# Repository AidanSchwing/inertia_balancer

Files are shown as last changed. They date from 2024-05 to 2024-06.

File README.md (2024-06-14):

# Inertia Balancer Project

**Author:** Aidan Schwing, Sydney Ulvick

https://aidanschwing.github.io/inertia_balancer/

# Introduction
An inverted pendulum is a classic example of an unstable, controllable system in control theory. These systems are typically created using either a movable base or a moving mass to control the position of the system. We set out to implement such a system with reaction wheel-based balancing.  Initial designs of the system included a servo to brake the spinning mass in order to “bounce” up and balance. Our team was mostly interested in the control system implementation, and as such we chose to use an off-the-shelf motor controller. An ODrive derivative was ultimately chosen to serve as the BLDC driver with a 650kv quad-copter motor for price and availability. We wanted to constrain the system size to something that could serve as a display on a desk, approximately 6x6”. The final design is presented below. 

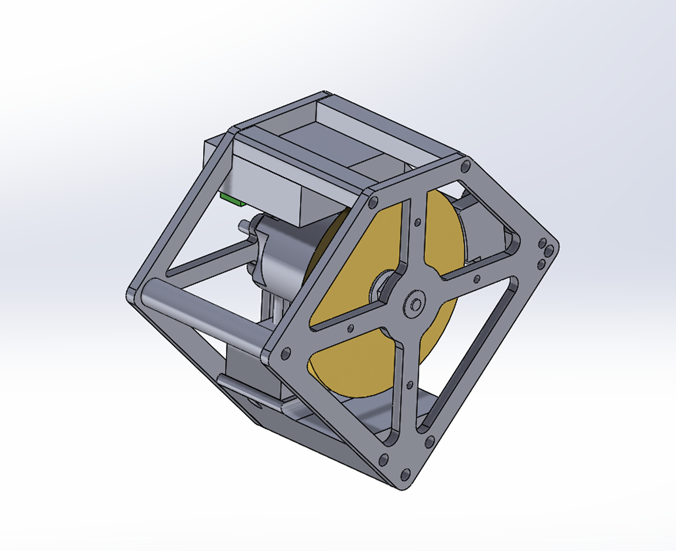
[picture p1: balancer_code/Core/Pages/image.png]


# Hardware

## Mechanical Hardware
The cube has a simple frame composed of two 3D printed sheets, separated by standoffs on four corners, fastened by M5 hardware. The inertia wheel is waterjet 6065 aluminum, post machined on the lathe to ensure concentricity with the motor shaft. The center hole was sized to ensure a light press fit on the motor shaft. The outer end of the motor shaft was turned to slide into a flanged bearing. The reaction wheel pressed into the motor shaft can be seen below, with its outer profile about to be turned to eliminate any eccentricity in the inertia.

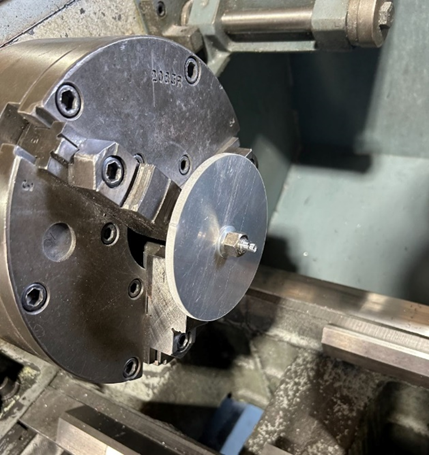
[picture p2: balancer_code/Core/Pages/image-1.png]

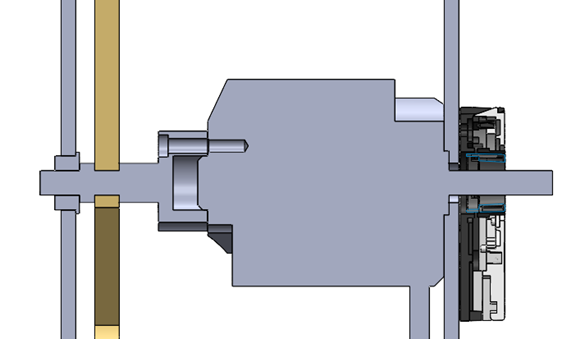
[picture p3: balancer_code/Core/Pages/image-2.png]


Motor selection was paramount for ensuring that the system would be able to output enough torque for balancing from relatively large angles. Referenced projects implement small, gimbal-style motors or extremely low kv quadcopter motors. Motor selection is interconnected with controller selection, as the controller has to be sized appropriately to meet current requirements. We settled on a 650kv quadcopter motor due to the low kv and ability to use an ODrive field-oriented-control (FOC).

Original plans for the project were to directly control wheel torque for the purposes of manipulating system angle. Torque output by the rotating wheel can be directly related to the system angle, as discussed later in the system modeling section. ODrive is an open-source system that has torque control capabilities. The ODrive’s lowest level of control occurs directly on torque, with velocity and position controls being cascaded in exterior loops. Accessing the inner loop allows us to most directly control the system. 

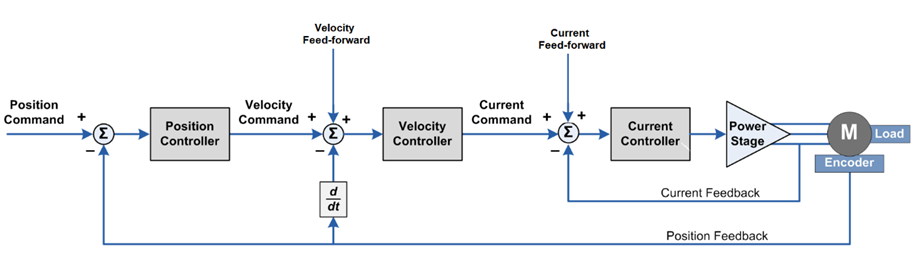
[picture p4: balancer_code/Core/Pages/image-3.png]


Upon exploration with real hardware, we discovered that the ODrive’s torque resolution is too low to control the system, driving us to use the velocity controller instead. This could potentially be resolved through use of a heavier flywheel or modifications to the controller hardware, but we did not have time to perfect the controller. 

## Electrical Hardware
To measure the angle of tilt, the ICM 20948 inertial measurement unit (IMU) was used. The imu was placed along the axis that we wanted the cube to balance along, allowing us to calculate system angle from 2 of the IMU axes. The result of this is the x direction pointing right and the y direction pointing up when the cube is upright. A depiction of the IMU orientation on the cube can be seen below. The chosen IMU has both I2C and SPI communication protocols; we chose to use I2C.  

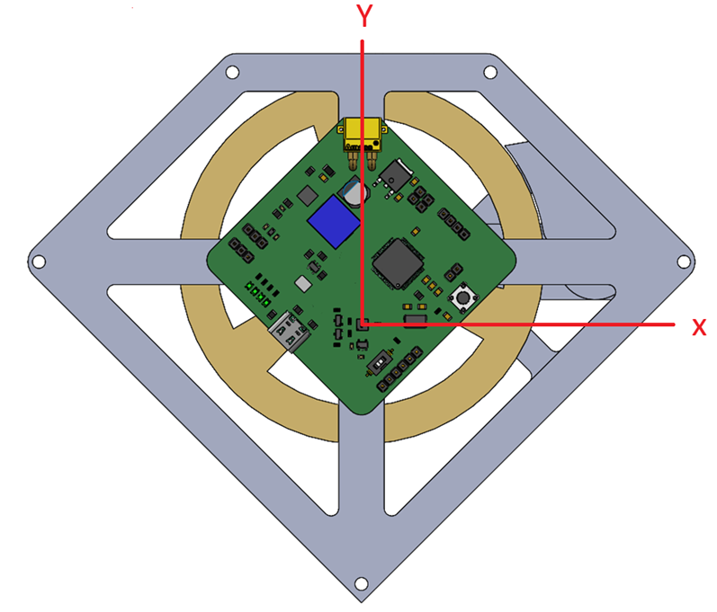
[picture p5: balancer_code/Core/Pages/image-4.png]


Interface between the motor controller and MCU PCB was accomplished with UART. This UART connection allows for reading and writing of almost every motor control parameter. Of note are direct speed and position readouts, which can be used for inputs to the LQR controller. 

The system was powered via a 4s1p, with 450 mAh, 75C max LiPO battery. The PCB was designed to interact with required sensors and motor drivers, and needed power provided appropriately. Input battery voltage (14.8V) was stepped to 5V via a buck regulator, then to 3.8V via a linear regulator for the MCU, then to 1.8V via another linear regulator for the IMU. Headers were included to power and interact with the servo, motor, motor driver, encoder, and remote e stop during troubleshooting and for worst-case if we were unable to get board power functional. Status LEDs for all voltage levels and as an MCU output were implemented. 

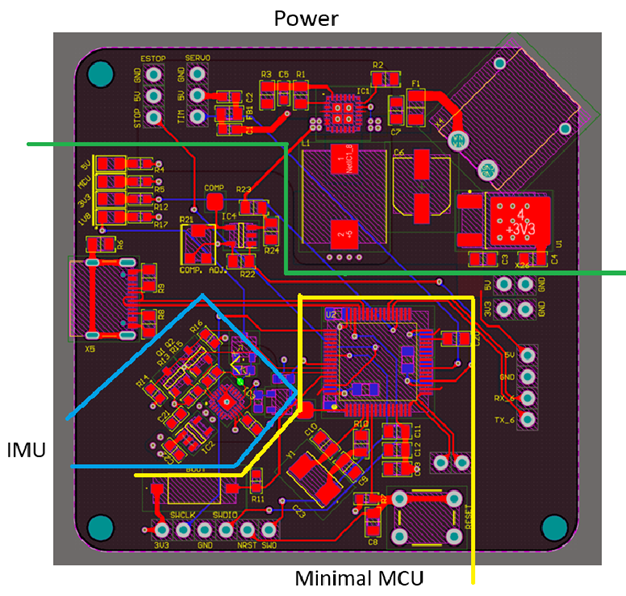
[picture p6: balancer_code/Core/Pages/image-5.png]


# Software Implementation
All code for this project was written in C. Tasks are implemented in a pseudo-state machine. The IMU state generates a new set of state variables that are used for calculation of the controller set-point in the reaction state. While they are drawn as dependent in Figure X, each of the states occurs only when a flag is set by a timer-based interrupt. Timer interrupts exist for both of the critical tasks and only raise a flag indicating that the task should be called. This ensures that the IMU read and reaction set-point recalculation occur at intervals that are approximately the same, but prevents the tasks from interrupting each other. If the set-point receives an invalid input, no speed is set. If the IMU state is missed, the control state simply outputs the same speed as the previous iteration. 

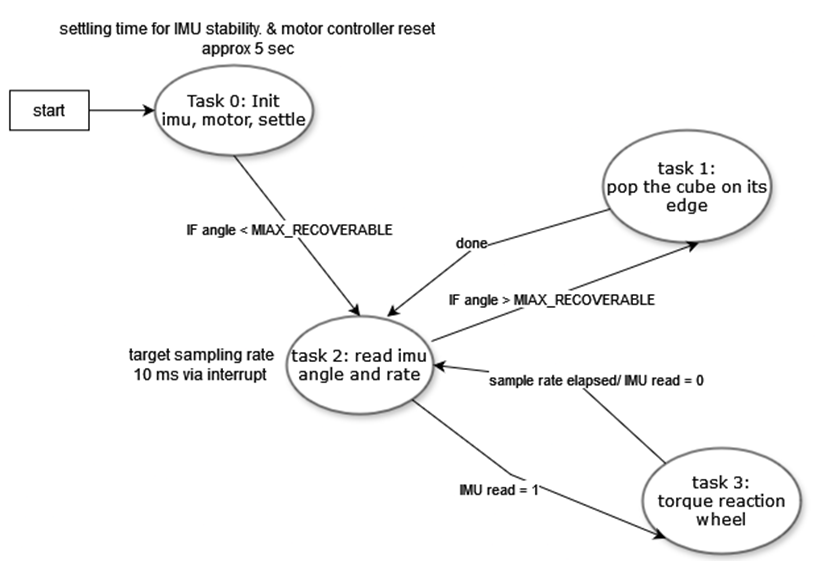
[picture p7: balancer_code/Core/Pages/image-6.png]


## IMU
An IMU driver was created from the ground up due to lack of available resources on its use with I2C. The initialization of the IMU checks the connection of the device and reads the device address. It then sends feedback through UART to a laptop. 

To best read the pitch angle, both accelerometer and gyroscope data were read. The gyroscope was read for short term accuracy but drifted through extended durations while accelerometer data was consistent but had significant noise. In order to get an accurate pitch angle over a long period of time, a complementary filter was implemented with an alpha of 0.98 on accelerometer readings. The pitch was read from the accelerometer by taking the inverse tan of the y and x components, knowing that gravity is always in the direction of negative y. The pitch from the gyro was read by integrating the value by multiplying it with the sampling rate. This setup requires the system to be “calibrated” by leaving the system near it’s zero point for approximately 3 seconds, allowing the calculated system angle to settle. 

Ultimately, it would have been easier to use an IMU with built-in euler angle calculations. 

## Motor Driver: ODrive Interface
Communication with the ODrive motor controller from a separate MCU is possible with a wide variety of protocols. The simplest of these is the [ASCII protocol](https://docs.odriverobotics.com/v/latest/manual/ascii-protocol.html) , where strings are sent in a specified format and terminated with a new-line character. This protocol allows for both writing and reading of control parameters for the BLDC. 

The ODrive also responds to some commands with specified outputs of known format. Receiving these responses is non-trivial and is performed with a callback on UART inputs that checks the length of a message buffer and for the termination character of the response. A blocking “receive” state is placed on the main code loop during message receives from the external controller, though this response period is usually negligibly short compared to other code critical code execution.  

## Control System
Multiple controllers were considered for optimally balancing. While PID control can be useful for driving the system to zero angle, it does allow for minimization of the spinning mass’s speed. An LQR controller can ideally perform multi-variate control, as the controlled variable can be treated as a function of the chosen state variables. An LQR controller can minimize system angle and wheel speed if optimized correctly. LQR controller implementation is also computationally inexpensive, as once the state variables are determined it is simply a matter of multiplying said state variables by their respective gains. 

The system was modeled using state variables of system angle, angular speed, and wheel angular speed. Due to the torque control issues mentioned in the mechanical hardware section, we switched the BLDC to control motor speed. We then can estimate the change in speed with some small time constant approximated from step tests in speed.

Once the state matrices were determined, MATLAB was used to discretize the system model and determine the LQR gains. The discretized system response appeared reasonable, but ultimately the gains failed to adequately control the system. 

Our largest issue with control was oscillations around zero angle. High penalty on system angle during LQR gain calculation results in very aggressive oscillations around the zero angle as error changes signs, while low penalty fails to adequately generate the torque required beyond a very small angle range. The system can balance for an extremely small range of angles, but further exploration into control strategies could prove beneficial to performance. Direct control over torque as originally planned would be best for system control, as the speed of the motor is not directly coupled with the system angle. 

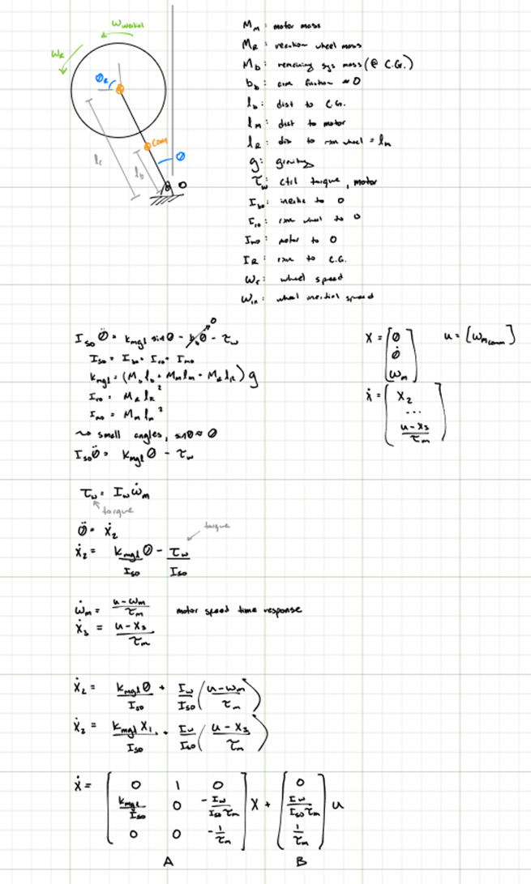
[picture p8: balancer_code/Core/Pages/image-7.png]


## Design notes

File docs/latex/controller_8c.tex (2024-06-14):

\doxysection{controller.\+c File Reference}
\hypertarget{controller_8c}{}\label{controller_8c}\index{controller.c@{controller.c}}

Provides functions relevant to system control.  

{\ttfamily \#include "{}controller.\+h"{}}\newline
{\ttfamily \#include "{}main.\+h"{}}\newline
{\ttfamily \#include $<$math.\+h$>$}\newline
Include dependency graph for controller.\+c\+:\nopagebreak
\begin{figure}[H]
\begin{center}
\leavevmode
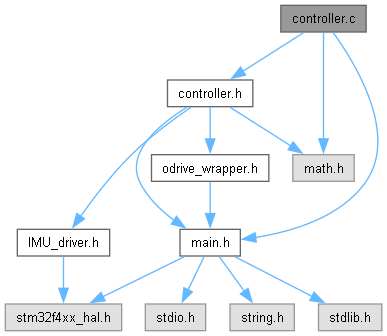
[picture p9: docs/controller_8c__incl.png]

\end{center}
\end{figure}
\doxysubsubsection*{Macros}
\begin{DoxyCompactItemize}
\item 
\#define \mbox{\hyperlink{controller_8c_a58a9c1a7ff5f19164ba9811c9fd80770}{MAX\+\_\+\+CHANGE}}~0.\+1
\begin{DoxyCompactList}\small\item\em Maximum change in controller speed setpoint per interval. \end{DoxyCompactList}\end{DoxyCompactItemize}
\doxysubsubsection*{Functions}
\begin{DoxyCompactItemize}
\item 
void \mbox{\hyperlink{controller_8c_a1bb07a75ed5a7889a5ccb8bc1ae6a9f6}{update\+\_\+control}} (\mbox{\hyperlink{structodrive__t}{odrive\+\_\+t}} \texorpdfstring{$\ast$}{*}p\+\_\+odrive, float angle, float \mbox{\hyperlink{controller_8c_acb4c2f4fbad69c2d11b5878671545191}{angular\+\_\+velocity}}, float motor\+\_\+curr\+\_\+speed)
\begin{DoxyCompactList}\small\item\em Calculates an updates the motor speed setpoint using an LQR implementation. \end{DoxyCompactList}\item 
\mbox{\hyperlink{structpos__spd}{pos\+\_\+spd}} \mbox{\hyperlink{controller_8c_a954bf1baac2fc318fb976257965a9940}{calculate\+\_\+\+IMU\+\_\+\+Angle}} (\mbox{\hyperlink{struct_i_c_m__20948}{ICM\+\_\+20948}} \texorpdfstring{$\ast$}{*}p\+\_\+\+IMU)
\begin{DoxyCompactList}\small\item\em Initializes the system angle using the IMU using a complementary filter. \end{DoxyCompactList}\end{DoxyCompactItemize}
\doxysubsubsection*{Variables}
\begin{DoxyCompactItemize}
\item 
float \mbox{\hyperlink{controller_8c_ab9495215123bd4bc532d4678cb402897}{K}} \mbox{[}3\mbox{]} = \{15, 0.\+1, -\/0.\+3\}
\begin{DoxyCompactList}\small\item\em LQR gain matrix. \end{DoxyCompactList}\item 
float \mbox{\hyperlink{controller_8c_ad50f9053a1bfede86c60be067d744d71}{x}} \mbox{[}3\mbox{]} = \{0,0,0\}
\begin{DoxyCompactList}\small\item\em State vector in form \mbox{[}angle, angular\+\_\+vel, wheel\+\_\+spd\mbox{]}. \end{DoxyCompactList}\item 
float \mbox{\hyperlink{controller_8c_a55831f7eab5ed2917a0191e858852f42}{u}} = 0
\begin{DoxyCompactList}\small\item\em Commanded motor speed. \end{DoxyCompactList}\item 
char \mbox{\hyperlink{controller_8c_a34e7004bcd98a060416abb58359410fd}{ctrl\+\_\+msg}} \mbox{[}50\mbox{]}
\item 
float \mbox{\hyperlink{controller_8c_a5be5be58449ccca7679ac2d151477f9d}{angle\+\_\+z}} = 0.\+0f
\item 
float \mbox{\hyperlink{controller_8c_acb4c2f4fbad69c2d11b5878671545191}{angular\+\_\+velocity}} = 0.\+0f
\end{DoxyCompactItemize}

\doxysubsection{Detailed Description}
Provides functions relevant to system control. 

\doxysubsection{Macro Definition Documentation}
\Hypertarget{controller_8c_a58a9c1a7ff5f19164ba9811c9fd80770}\index{controller.c@{controller.c}!MAX\_CHANGE@{MAX\_CHANGE}}
\index{MAX\_CHANGE@{MAX\_CHANGE}!controller.c@{controller.c}}
\doxysubsubsection{\texorpdfstring{MAX\_CHANGE}{MAX\_CHANGE}}
{\footnotesize\ttfamily \label{controller_8c_a58a9c1a7ff5f19164ba9811c9fd80770} 
\#define MAX\+\_\+\+CHANGE~0.\+1}

Maximum change in controller speed setpoint per interval. 

\doxysubsection{Function Documentation}
\Hypertarget{controller_8c_a954bf1baac2fc318fb976257965a9940}\index{controller.c@{controller.c}!calculate\_IMU\_Angle@{calculate\_IMU\_Angle}}
\index{calculate\_IMU\_Angle@{calculate\_IMU\_Angle}!controller.c@{controller.c}}
\doxysubsubsection{\texorpdfstring{calculate\_IMU\_Angle()}{calculate\_IMU\_Angle()}}
{\footnotesize\ttfamily \label{controller_8c_a954bf1baac2fc318fb976257965a9940} 
\mbox{\hyperlink{structpos__spd}{pos\+\_\+spd}} calculate\+\_\+\+IMU\+\_\+\+Angle (\begin{DoxyParamCaption}\item[{\mbox{\hyperlink{struct_i_c_m__20948}{ICM\+\_\+20948}} \texorpdfstring{$\ast$}{*}}]{p\+\_\+\+IMU}{}\end{DoxyParamCaption})}

Initializes the system angle using the IMU using a complementary filter. 

Calls functions from the IMU driver and calculates the system angle using a complementary filter. Noise was determined to be substantial even in the gyro data, so the gyro output is smoothed by calculating the true change in system angle. This is a little messy. 
\begin{DoxyParams}{Parameters}
{\em \doxylink{struct_i_c_m__20948}{ICM\+\_\+20948}} & Pointer to an IMU object \\
\hline
\end{DoxyParams}
\Hypertarget{controller_8c_a1bb07a75ed5a7889a5ccb8bc1ae6a9f6}\index{controller.c@{controller.c}!update\_control@{update\_control}}
\index{update\_control@{update\_control}!controller.c@{controller.c}}
\doxysubsubsection{\texorpdfstring{update\_control()}{update\_control()}}
{\footnotesize\ttfamily \label{controller_8c_a1bb07a75ed5a7889a5ccb8bc1ae6a9f6} 
void update\+\_\+control (\begin{DoxyParamCaption}\item[{\mbox{\hyperlink{structodrive__t}{odrive\+\_\+t}} \texorpdfstring{$\ast$}{*}}]{p\+\_\+odrive}{, }\item[{float}]{angle}{, }\item[{float}]{angular\+\_\+velocity}{, }\item[{float}]{motor\+\_\+curr\+\_\+speed}{}\end{DoxyParamCaption})}

Calculates an updates the motor speed setpoint using an LQR implementation. 

Calculates the next motor speed setpoint using current state vector and set of LQR gains. LQR gains originally calculated using MATLAB script. 
\begin{DoxyParams}{Parameters}
{\em p\+\_\+odrive} & Pointer to an ODrive object. \\
\hline
{\em angle} & Current system angle. \\
\hline
{\em angular\+\_\+velocity} & Current system angular velocity. \\
\hline
{\em motor\+\_\+curr\+\_\+speed} & Current motor speed. \\
\hline
\end{DoxyParams}

\doxysubsection{Variable Documentation}
\Hypertarget{controller_8c_a5be5be58449ccca7679ac2d151477f9d}\index{controller.c@{controller.c}!angle\_z@{angle\_z}}
\index{angle\_z@{angle\_z}!controller.c@{controller.c}}
\doxysubsubsection{\texorpdfstring{angle\_z}{angle\_z}}
{\footnotesize\ttfamily \label{controller_8c_a5be5be58449ccca7679ac2d151477f9d} 
float angle\+\_\+z = 0.\+0f}

\Hypertarget{controller_8c_acb4c2f4fbad69c2d11b5878671545191}\index{controller.c@{controller.c}!angular\_velocity@{angular\_velocity}}
\index{angular\_velocity@{angular\_velocity}!controller.c@{controller.c}}
\doxysubsubsection{\texorpdfstring{angular\_velocity}{angular\_velocity}}
{\footnotesize\ttfamily \label{controller_8c_acb4c2f4fbad69c2d11b5878671545191} 
float angular\+\_\+velocity = 0.\+0f}

\Hypertarget{controller_8c_a34e7004bcd98a060416abb58359410fd}\index{controller.c@{controller.c}!ctrl\_msg@{ctrl\_msg}}
\index{ctrl\_msg@{ctrl\_msg}!controller.c@{controller.c}}
\doxysubsubsection{\texorpdfstring{ctrl\_msg}{ctrl\_msg}}
{\footnotesize\ttfamily \label{controller_8c_a34e7004bcd98a060416abb58359410fd} 
char ctrl\+\_\+msg\mbox{[}50\mbox{]}}

\Hypertarget{controller_8c_ab9495215123bd4bc532d4678cb402897}\index{controller.c@{controller.c}!K@{K}}
\index{K@{K}!controller.c@{controller.c}}
\doxysubsubsection{\texorpdfstring{K}{K}}
{\footnotesize\ttfamily \label{controller_8c_ab9495215123bd4bc532d4678cb402897} 
float K\mbox{[}3\mbox{]} = \{15, 0.\+1, -\/0.\+3\}}

LQR gain matrix. 

\Hypertarget{controller_8c_a55831f7eab5ed2917a0191e858852f42}\index{controller.c@{controller.c}!u@{u}}
\index{u@{u}!controller.c@{controller.c}}
\doxysubsubsection{\texorpdfstring{u}{u}}
{\footnotesize\ttfamily \label{controller_8c_a55831f7eab5ed2917a0191e858852f42} 
float u = 0}

Commanded motor speed. 

\Hypertarget{controller_8c_ad50f9053a1bfede86c60be067d744d71}\index{controller.c@{controller.c}!x@{x}}
\index{x@{x}!controller.c@{controller.c}}
\doxysubsubsection{\texorpdfstring{x}{x}}
{\footnotesize\ttfamily \label{controller_8c_ad50f9053a1bfede86c60be067d744d71} 
float x\mbox{[}3\mbox{]} = \{0,0,0\}}

State vector in form \mbox{[}angle, angular\+\_\+vel, wheel\+\_\+spd\mbox{]}.

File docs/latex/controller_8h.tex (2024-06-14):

\doxysection{controller.\+h File Reference}
\hypertarget{controller_8h}{}\label{controller_8h}\index{controller.h@{controller.h}}
{\ttfamily \#include "{}main.\+h"{}}\newline
{\ttfamily \#include "{}IMU\+\_\+driver.\+h"{}}\newline
{\ttfamily \#include "{}odrive\+\_\+wrapper.\+h"{}}\newline
{\ttfamily \#include $<$math.\+h$>$}\newline
Include dependency graph for controller.\+h\+:\nopagebreak
\begin{figure}[H]
\begin{center}
\leavevmode
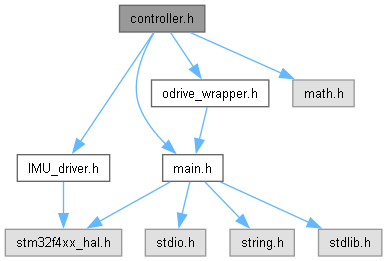
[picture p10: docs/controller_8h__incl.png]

\end{center}
\end{figure}
This graph shows which files directly or indirectly include this file\+:\nopagebreak
\begin{figure}[H]
\begin{center}
\leavevmode

\end{center}
\end{figure}
\doxysubsubsection*{Data Structures}
\begin{DoxyCompactItemize}
\item 
struct \mbox{\hyperlink{structpos__spd}{pos\+\_\+spd}}
\end{DoxyCompactItemize}
\doxysubsubsection*{Macros}
\begin{DoxyCompactItemize}
\item 
\#define \mbox{\hyperlink{controller_8h_af5abd28c44c29b7397c84f1fec4b1d84}{ALPHA}}~0.\+98
\item 
\#define \mbox{\hyperlink{controller_8h_a943f07034774ef1261d62cd0d3d1fec9}{DT}}~0.\+01
\item 
\#define \mbox{\hyperlink{controller_8h_ae13192d02ea165e8b1ac471bf287be16}{DISPLACEMENT\+\_\+\+DIST}}~0.\+07
\end{DoxyCompactItemize}
\doxysubsubsection*{Functions}
\begin{DoxyCompactItemize}
\item 
void \mbox{\hyperlink{controller_8h_a1bb07a75ed5a7889a5ccb8bc1ae6a9f6}{update\+\_\+control}} (\mbox{\hyperlink{structodrive__t}{odrive\+\_\+t}} \texorpdfstring{$\ast$}{*}p\+\_\+odrive, float angle, float \mbox{\hyperlink{controller_8c_acb4c2f4fbad69c2d11b5878671545191}{angular\+\_\+velocity}}, float motor\+\_\+curr\+\_\+speed)
\begin{DoxyCompactList}\small\item\em Calculates an updates the motor speed setpoint using an LQR implementation. \end{DoxyCompactList}\item 
\mbox{\hyperlink{structpos__spd}{pos\+\_\+spd}} \mbox{\hyperlink{controller_8h_a954bf1baac2fc318fb976257965a9940}{calculate\+\_\+\+IMU\+\_\+\+Angle}} (\mbox{\hyperlink{struct_i_c_m__20948}{ICM\+\_\+20948}} \texorpdfstring{$\ast$}{*}p\+\_\+\+IMU)
\begin{DoxyCompactList}\small\item\em Initializes the system angle using the IMU using a complementary filter. \end{DoxyCompactList}\end{DoxyCompactItemize}
\doxysubsubsection*{Variables}
\begin{DoxyCompactItemize}
\item 
struct pos\+\_\+spd \mbox{\hyperlink{controller_8h_a739745815516ab387b3bd08e33ddc4c3}{pos\+\_\+spd}}
\end{DoxyCompactItemize}

\doxysubsection{Macro Definition Documentation}
\Hypertarget{controller_8h_af5abd28c44c29b7397c84f1fec4b1d84}\index{controller.h@{controller.h}!ALPHA@{ALPHA}}
\index{ALPHA@{ALPHA}!controller.h@{controller.h}}
\doxysubsubsection{\texorpdfstring{ALPHA}{ALPHA}}
{\footnotesize\ttfamily \label{controller_8h_af5abd28c44c29b7397c84f1fec4b1d84} 
\#define ALPHA~0.\+98}

\Hypertarget{controller_8h_ae13192d02ea165e8b1ac471bf287be16}\index{controller.h@{controller.h}!DISPLACEMENT\_DIST@{DISPLACEMENT\_DIST}}
\index{DISPLACEMENT\_DIST@{DISPLACEMENT\_DIST}!controller.h@{controller.h}}
\doxysubsubsection{\texorpdfstring{DISPLACEMENT\_DIST}{DISPLACEMENT\_DIST}}
{\footnotesize\ttfamily \label{controller_8h_ae13192d02ea165e8b1ac471bf287be16} 
\#define DISPLACEMENT\+\_\+\+DIST~0.\+07}

\Hypertarget{controller_8h_a943f07034774ef1261d62cd0d3d1fec9}\index{controller.h@{controller.h}!DT@{DT}}
\index{DT@{DT}!controller.h@{controller.h}}
\doxysubsubsection{\texorpdfstring{DT}{DT}}
{\footnotesize\ttfamily \label{controller_8h_a943f07034774ef1261d62cd0d3d1fec9} 
\#define DT~0.\+01}

\doxysubsection{Function Documentation}
\Hypertarget{controller_8h_a954bf1baac2fc318fb976257965a9940}\index{controller.h@{controller.h}!calculate\_IMU\_Angle@{calculate\_IMU\_Angle}}
\index{calculate\_IMU\_Angle@{calculate\_IMU\_Angle}!controller.h@{controller.h}}
\doxysubsubsection{\texorpdfstring{calculate\_IMU\_Angle()}{calculate\_IMU\_Angle()}}
{\footnotesize\ttfamily \label{controller_8h_a954bf1baac2fc318fb976257965a9940} 
\mbox{\hyperlink{structpos__spd}{pos\+\_\+spd}} calculate\+\_\+\+IMU\+\_\+\+Angle (\begin{DoxyParamCaption}\item[{\mbox{\hyperlink{struct_i_c_m__20948}{ICM\+\_\+20948}} \texorpdfstring{$\ast$}{*}}]{p\+\_\+\+IMU}{}\end{DoxyParamCaption})}

Initializes the system angle using the IMU using a complementary filter. 

Calls functions from the IMU driver and calculates the system angle using a complementary filter. Noise was determined to be substantial even in the gyro data, so the gyro output is smoothed by calculating the true change in system angle. This is a little messy. 
\begin{DoxyParams}{Parameters}
{\em \doxylink{struct_i_c_m__20948}{ICM\+\_\+20948}} & Pointer to an IMU object \\
\hline
\end{DoxyParams}
\Hypertarget{controller_8h_a1bb07a75ed5a7889a5ccb8bc1ae6a9f6}\index{controller.h@{controller.h}!update\_control@{update\_control}}
\index{update\_control@{update\_control}!controller.h@{controller.h}}
\doxysubsubsection{\texorpdfstring{update\_control()}{update\_control()}}
{\footnotesize\ttfamily \label{controller_8h_a1bb07a75ed5a7889a5ccb8bc1ae6a9f6} 
void update\+\_\+control (\begin{DoxyParamCaption}\item[{\mbox{\hyperlink{structodrive__t}{odrive\+\_\+t}} \texorpdfstring{$\ast$}{*}}]{p\+\_\+odrive}{, }\item[{float}]{angle}{, }\item[{float}]{angular\+\_\+velocity}{, }\item[{float}]{motor\+\_\+curr\+\_\+speed}{}\end{DoxyParamCaption})}

Calculates an updates the motor speed setpoint using an LQR implementation. 

Calculates the next motor speed setpoint using current state vector and set of LQR gains. LQR gains originally calculated using MATLAB script. 
\begin{DoxyParams}{Parameters}
{\em p\+\_\+odrive} & Pointer to an ODrive object. \\
\hline
{\em angle} & Current system angle. \\
\hline
{\em angular\+\_\+velocity} & Current system angular velocity. \\
\hline
{\em motor\+\_\+curr\+\_\+speed} & Current motor speed. \\
\hline
\end{DoxyParams}

\doxysubsection{Variable Documentation}
\Hypertarget{controller_8h_a739745815516ab387b3bd08e33ddc4c3}\index{controller.h@{controller.h}!pos\_spd@{pos\_spd}}
\index{pos\_spd@{pos\_spd}!controller.h@{controller.h}}
\doxysubsubsection{\texorpdfstring{pos\_spd}{pos\_spd}}
{\footnotesize\ttfamily \label{controller_8h_a739745815516ab387b3bd08e33ddc4c3} 
struct pos\+\_\+spd pos\+\_\+spd}

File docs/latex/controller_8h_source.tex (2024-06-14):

\doxysection{controller.\+h}
\hypertarget{controller_8h_source}{}\label{controller_8h_source}\index{controller.h@{controller.h}}
\mbox{\hyperlink{controller_8h}{Go to the documentation of this file.}}
\begin{DoxyCode}{0}
\DoxyCodeLine{00001\ \textcolor{comment}{/*}}
\DoxyCodeLine{00002\ \textcolor{comment}{\ *\ controller.h}}
\DoxyCodeLine{00003\ \textcolor{comment}{\ *}}
\DoxyCodeLine{00004\ \textcolor{comment}{\ *\ \ Created\ on:\ Jun\ 8,\ 2024}}
\DoxyCodeLine{00005\ \textcolor{comment}{\ *\ \ \ \ \ \ Author:\ Aidan}}
\DoxyCodeLine{00006\ \textcolor{comment}{\ */}}
\DoxyCodeLine{00007\ }
\DoxyCodeLine{00008\ \textcolor{preprocessor}{\#ifndef\ INC\_CONTROLLER\_H\_}}
\DoxyCodeLine{00009\ \textcolor{preprocessor}{\#define\ INC\_CONTROLLER\_H\_}}
\DoxyCodeLine{00010\ }
\DoxyCodeLine{00011\ \textcolor{preprocessor}{\#include\ "{}\mbox{\hyperlink{main_8h}{main.h}}"{}}}
\DoxyCodeLine{00012\ \textcolor{preprocessor}{\#include\ "{}\mbox{\hyperlink{_i_m_u__driver_8h}{IMU\_driver.h}}"{}}}
\DoxyCodeLine{00013\ \textcolor{preprocessor}{\#include\ "{}\mbox{\hyperlink{odrive__wrapper_8h}{odrive\_wrapper.h}}"{}}}
\DoxyCodeLine{00014\ \textcolor{preprocessor}{\#include\ <math.h>}}
\DoxyCodeLine{00015\ }
\DoxyCodeLine{00016\ \textcolor{comment}{//\ defines\ for\ the\ complementary\ filter}}
\DoxyCodeLine{00017\ \textcolor{preprocessor}{\#define\ ALPHA\ 0.98}}
\DoxyCodeLine{00018\ \textcolor{preprocessor}{\#define\ DT\ 0.01\ \ \ \ \ \ \ \ \ \ \ \ \ \ \ \ \ \ \ \ \ }\textcolor{comment}{//\ sampling\ period\ 10ms}}
\DoxyCodeLine{00019\ \textcolor{preprocessor}{\#define\ DISPLACEMENT\_DIST\ 0.07\ \ \ \ \ \ }\textcolor{comment}{//\ displacement\ distance\ to\ the\ axis\ of\ the\ gyro\ that\ is}}
\DoxyCodeLine{00020\ }
\DoxyCodeLine{00021\ \textcolor{keyword}{struct\ }\mbox{\hyperlink{structpos__spd}{pos\_spd}}\ \{}
\DoxyCodeLine{00022\ \ \ \ \ \textcolor{keywordtype}{float}\ \mbox{\hyperlink{structpos__spd_a76777b356ab2a080225682528119c4fe}{position}};}
\DoxyCodeLine{00023\ \ \ \ \ \textcolor{keywordtype}{float}\ \mbox{\hyperlink{structpos__spd_a7f7e4724cf57d59513b39c5ecc81adc8}{speed}};}
\DoxyCodeLine{00024\ \}\textcolor{keyword}{typedef}\ \mbox{\hyperlink{controller_8h_a739745815516ab387b3bd08e33ddc4c3}{pos\_spd}};}
\DoxyCodeLine{00025\ }
\DoxyCodeLine{00026\ \textcolor{comment}{//\ prototype\ functions}}
\DoxyCodeLine{00027\ \textcolor{comment}{//\ LQR\ controller,\ update\ speed\ setpoint}}
\DoxyCodeLine{00028\ \textcolor{keywordtype}{void}\ \mbox{\hyperlink{controller_8h_a1bb07a75ed5a7889a5ccb8bc1ae6a9f6}{update\_control}}(\mbox{\hyperlink{structodrive__t}{odrive\_t}}\ *p\_odrive,\ \textcolor{keywordtype}{float}\ angle,\ \textcolor{keywordtype}{float}\ \mbox{\hyperlink{controller_8c_acb4c2f4fbad69c2d11b5878671545191}{angular\_velocity}},\ \textcolor{keywordtype}{float}\ motor\_curr\_speed);}
\DoxyCodeLine{00029\ \textcolor{comment}{//\ System\ angle\ using\ complementary\ filter\ on\ gyro\ and\ accel\ data}}
\DoxyCodeLine{00030\ \mbox{\hyperlink{structpos__spd}{pos\_spd}}\ \mbox{\hyperlink{controller_8h_a954bf1baac2fc318fb976257965a9940}{calculate\_IMU\_Angle}}(\mbox{\hyperlink{struct_i_c_m__20948}{ICM\_20948}}\ *p\_IMU);}
\DoxyCodeLine{00031\ }
\DoxyCodeLine{00032\ }
\DoxyCodeLine{00033\ \textcolor{preprocessor}{\#endif\ }\textcolor{comment}{/*\ INC\_CONTROLLER\_H\_\ */}\textcolor{preprocessor}{}}

\end{DoxyCode}

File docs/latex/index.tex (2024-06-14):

\chapter{reaction\+\_\+balance}
\hypertarget{index}{}\label{index}\index{reaction\_balance@{reaction\_balance}}
{\bfseries{Author\+:}} Aidan Schwing, Sydney Ulvick

{\bfseries{Date\+:}} 2024-\/06-\/14\hypertarget{index_autotoc_md0}{}\doxysection{\texorpdfstring{Introduction}{Introduction}}\label{index_autotoc_md0}
An inverted pendulum is a classic example of an unstable, controllable system in control theory. These systems are typically created using either a movable base or a moving mass to control the position of the system. We set out to implement such a system with reaction wheel-\/based balancing. Initial designs of the system included a servo to brake the spinning mass in order to “bounce” up and balance. Our team was mostly interested in the control system implementation, and as such we chose to use an off-\/the-\/shelf motor controller. An ODrive derivative was ultimately chosen to serve as the BLDC driver with a 650kv quad-\/copter motor for price and availability. We wanted to constrain the system size to something that could serve as a display on a desk, approximately 6x6”. The final design is presented below.

\hypertarget{index_autotoc_md1}{}\doxysection{\texorpdfstring{Hardware}{Hardware}}\label{index_autotoc_md1}
\hypertarget{index_autotoc_md2}{}\doxysubsection{\texorpdfstring{Mechanical Hardware}{Mechanical Hardware}}\label{index_autotoc_md2}
The cube has a simple frame composed of two 3D printed sheets, separated by standoffs on four corners, fastened by M5 hardware. The inertia wheel is waterjet 6065 aluminum, post machined on the lathe to ensure concentricity with the motor shaft. The center hole was sized to ensure a light press fit on the motor shaft. The outer end of the motor shaft was turned to slide into a flanged bearing. The reaction wheel pressed into the motor shaft can be seen below, with its outer profile about to be turned to eliminate any eccentricity in the inertia.

Motor selection was paramount for ensuring that the system would be able to output enough torque for balancing from relatively large angles. Referenced projects implement small, gimbal-\/style motors or extremely low kv quadcopter motors. Motor selection is interconnected with controller selection, as the controller has to be sized appropriately to meet current requirements. We settled on a 650kv quadcopter motor due to the low kv and ability to use an ODrive field-\/oriented-\/control (FOC).

Original plans for the project were to directly control wheel torque for the purposes of manipulating system angle. Torque output by the rotating wheel can be directly related to the system angle, as discussed later in the system modeling section. ODrive is an open-\/source system that has torque control capabilities. The ODrive’s lowest level of control occurs directly on torque, with velocity and position controls being cascaded in exterior loops. Accessing the inner loop allows us to most directly control the system.

Upon exploration with real hardware, we discovered that the ODrive’s torque resolution is too low to control the system, driving us to use the velocity controller instead. This could potentially be resolved through use of a heavier flywheel or modifications to the controller hardware, but we did not have time to perfect the controller.\hypertarget{index_autotoc_md3}{}\doxysubsection{\texorpdfstring{Electrical Hardware}{Electrical Hardware}}\label{index_autotoc_md3}
To measure the angle of tilt, the ICM 20948 inertial measurement unit (IMU) was used. The imu was placed along the axis that we wanted the cube to balance along, allowing us to calculate system angle from 2 of the IMU axes. The result of this is the x direction pointing right and the y direction pointing up when the cube is upright. A depiction of the IMU orientation on the cube can be seen below. The chosen IMU has both I2C and SPI communication protocols; we chose to use I2C. ~\newline

Interface between the motor controller and MCU PCB was accomplished with UART. This UART connection allows for reading and writing of almost every motor control parameter. Of note are direct speed and position readouts, which can be used for inputs to the LQR controller.

The system was powered via a 4s1p, with 450 m\+Ah, 75C max Li\+PO battery. The PCB was designed to interact with required sensors and motor drivers, and needed power provided appropriately. Input battery voltage (14.\+8V) was stepped to 5V via a buck regulator, then to 3.\+8V via a linear regulator for the MCU, then to 1.\+8V via another linear regulator for the IMU. Headers were included to power and interact with the servo, motor, motor driver, encoder, and remote e stop during troubleshooting and for worst-\/case if we were unable to get board power functional. Status LEDs for all voltage levels and as an MCU output were implemented.

\hypertarget{index_autotoc_md4}{}\doxysection{\texorpdfstring{Software Implementation}{Software Implementation}}\label{index_autotoc_md4}
All code for this project was written in C. Tasks are implemented in a pseudo-\/state machine. The IMU state generates a new set of state variables that are used for calculation of the controller set-\/point in the reaction state. While they are drawn as dependent in Figure X, each of the states occurs only when a flag is set by a timer-\/based interrupt. Timer interrupts exist for both of the critical tasks and only raise a flag indicating that the task should be called. This ensures that the IMU read and reaction set-\/point recalculation occur at intervals that are approximately the same, but prevents the tasks from interrupting each other. If the set-\/point receives an invalid input, no speed is set. If the IMU state is missed, the control state simply outputs the same speed as the previous iteration.

\hypertarget{index_autotoc_md5}{}\doxysubsection{\texorpdfstring{IMU}{IMU}}\label{index_autotoc_md5}
An IMU driver was created from the ground up due to lack of available resources on its use with I2C. The initialization of the IMU checks the connection of the device and reads the device address. It then sends feedback through UART to a laptop.

To best read the pitch angle, both accelerometer and gyroscope data were read. The gyroscope was read for short term accuracy but drifted through extended durations while accelerometer data was consistent but had significant noise. In order to get an accurate pitch angle over a long period of time, a complementary filter was implemented with an alpha of 0.\+98 on accelerometer readings. The pitch was read from the accelerometer by taking the inverse tan of the y and x components, knowing that gravity is always in the direction of negative y. The pitch from the gyro was read by integrating the value by multiplying it with the sampling rate. This setup requires the system to be “calibrated” by leaving the system near it’s zero point for approximately 3 seconds, allowing the calculated system angle to settle.

Ultimately, it would have been easier to use an IMU with built-\/in euler angle calculations.\hypertarget{index_autotoc_md6}{}\doxysubsection{\texorpdfstring{Motor Driver\+: ODrive Interface}{Motor Driver\+: ODrive Interface}}\label{index_autotoc_md6}
Communication with the ODrive motor controller from a separate MCU is possible with a wide variety of protocols. The simplest of these is the \href{https://docs.odriverobotics.com/v/latest/manual/ascii-protocol.html}{\texttt{ ASCII protocol}} , where strings are sent in a specified format and terminated with a new-\/line character. This protocol allows for both writing and reading of control parameters for the BLDC.

The ODrive also responds to some commands with specified outputs of known format. Receiving these responses is non-\/trivial and is performed with a callback on UART inputs that checks the length of a message buffer and for the termination character of the response. A blocking “receive” state is placed on the main code loop during message receives from the external controller, though this response period is usually negligibly short compared to other code critical code execution. ~\newline
\hypertarget{index_autotoc_md7}{}\doxysubsection{\texorpdfstring{Control System}{Control System}}\label{index_autotoc_md7}
Multiple controllers were considered for optimally balancing. While PID control can be useful for driving the system to zero angle, it does allow for minimization of the spinning mass’s speed. An LQR controller can ideally perform multi-\/variate control, as the controlled variable can be treated as a function of the chosen state variables. An LQR controller can minimize system angle and wheel speed if optimized correctly. LQR controller implementation is also computationally inexpensive, as once the state variables are determined it is simply a matter of multiplying said state variables by their respective gains.

The system was modeled using state variables of system angle, angular speed, and wheel angular speed. Due to the torque control issues mentioned in the mechanical hardware section, we switched the BLDC to control motor speed. We then can estimate the change in speed with some small time constant approximated from step tests in speed.

Once the state matrices were determined, MATLAB was used to discretize the system model and determine the LQR gains. The discretized system response appeared reasonable, but ultimately the gains failed to adequately control the system.

Our largest issue with control was oscillations around zero angle. High penalty on system angle during LQR gain calculation results in very aggressive oscillations around the zero angle as error changes signs, while low penalty fails to adequately generate the torque required beyond a very small angle range. The system can balance for an extremely small range of angles, but further exploration into control strategies could prove beneficial to performance. Direct control over torque as originally planned would be best for system control, as the speed of the motor is not directly coupled with the system angle.

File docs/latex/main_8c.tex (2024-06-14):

\doxysection{main.\+c File Reference}
\hypertarget{main_8c}{}\label{main_8c}\index{main.c@{main.c}}

Main program body.  

{\ttfamily \#include "{}main.\+h"{}}\newline
{\ttfamily \#include "{}odrive\+\_\+wrapper.\+h"{}}\newline
{\ttfamily \#include "{}IMU\+\_\+driver.\+h"{}}\newline
{\ttfamily \#include "{}controller.\+h"{}}\newline
{\ttfamily \#include "{}rc\+\_\+input.\+h"{}}\newline
{\ttfamily \#include $<$math.\+h$>$}\newline
Include dependency graph for main.\+c\+:\nopagebreak
\begin{figure}[H]
\begin{center}
\leavevmode

\end{center}
\end{figure}
\doxysubsubsection*{Functions}
\begin{DoxyCompactItemize}
\item 
void \mbox{\hyperlink{main_8c_a70af21c671abfcc773614a9a4f63d920}{System\+Clock\+\_\+\+Config}} (void)
\begin{DoxyCompactList}\small\item\em System Clock Configuration. \end{DoxyCompactList}\item 
int \mbox{\hyperlink{main_8c_a840291bc02cba5474a4cb46a9b9566fe}{main}} (void)
\begin{DoxyCompactList}\small\item\em The application entry point. \end{DoxyCompactList}\item 
void \mbox{\hyperlink{main_8c_ae494a9643f29b87d6d81e5264e60e57b}{HAL\+\_\+\+UART\+\_\+\+Rx\+Cplt\+Callback}} (UART\+\_\+\+Handle\+Type\+Def \texorpdfstring{$\ast$}{*}huart)
\item 
void \mbox{\hyperlink{main_8c_a8a3b0ad512a6e6c6157440b68d395eac}{HAL\+\_\+\+TIM\+\_\+\+Period\+Elapsed\+Callback}} (TIM\+\_\+\+Handle\+Type\+Def \texorpdfstring{$\ast$}{*}htim)
\item 
void \mbox{\hyperlink{main_8c_a1730ffe1e560465665eb47d9264826f9}{Error\+\_\+\+Handler}} (void)
\begin{DoxyCompactList}\small\item\em This function is executed in case of error occurrence. \end{DoxyCompactList}\end{DoxyCompactItemize}
\doxysubsubsection*{Variables}
\begin{DoxyCompactItemize}
\item 
I2\+C\+\_\+\+Handle\+Type\+Def \mbox{\hyperlink{main_8c_af7b2c26e44dadaaa798a5c3d82914ba7}{hi2c1}}
\item 
TIM\+\_\+\+Handle\+Type\+Def \mbox{\hyperlink{main_8c_a25fc663547539bc49fecc0011bd76ab5}{htim1}}
\item 
TIM\+\_\+\+Handle\+Type\+Def \mbox{\hyperlink{main_8c_aac3d2c59ee0e3bbae1b99529a154eb62}{htim3}}
\item 
TIM\+\_\+\+Handle\+Type\+Def \mbox{\hyperlink{main_8c_a85788cec5a97ee377e4ee2e74f026484}{htim4}}
\item 
TIM\+\_\+\+Handle\+Type\+Def \mbox{\hyperlink{main_8c_acefaeaaa3856ddddae7083b2d220fe4b}{htim5}}
\item 
TIM\+\_\+\+Handle\+Type\+Def \mbox{\hyperlink{main_8c_a2f22f985c4f33318fdcd4cc996623bf4}{htim11}}
\item 
UART\+\_\+\+Handle\+Type\+Def \mbox{\hyperlink{main_8c_aa9479c261d65eecedd3d9582f7f0f89c}{huart2}}
\item 
UART\+\_\+\+Handle\+Type\+Def \mbox{\hyperlink{main_8c_a38905dda1d2fbff006c69db48eddba9d}{huart6}}
\item 
\mbox{\hyperlink{structodrive__t}{odrive\+\_\+t}} \mbox{\hyperlink{main_8c_ad04fe84a2d499fe57651a80bf68f29de}{odrive}}
\item 
\mbox{\hyperlink{structodrive__t}{odrive\+\_\+t}} \mbox{\hyperlink{main_8c_a83ba99daa490dd49340550bb6fe885ba}{laptop}}
\item 
\mbox{\hyperlink{struct_i_c_m__20948}{ICM\+\_\+20948}} \mbox{\hyperlink{main_8c_a7c7b65fcf7197ae90670cd87ae675e95}{IMU}}
\item 
uint8\+\_\+t \mbox{\hyperlink{main_8c_ad7394d71a5b03e693a17bc6ea557b4d9}{rx\+Buffer}}
\item 
uint8\+\_\+t \mbox{\hyperlink{main_8c_a5f39e47fdf46ecf4822ca9875f6aacf3}{rx\+Index}}
\item 
uint8\+\_\+t \mbox{\hyperlink{main_8c_a20bc908e26cf958e1df3790d425cdb40}{response\+Finished\+Flag}}
\item 
uint8\+\_\+t \mbox{\hyperlink{main_8c_a076a5923dcfdcf95d91a8e24981ba4ee}{received\+Data}}
\item 
char \mbox{\hyperlink{main_8c_af4d22e2e3395f74933e838aa8134e4a3}{transmit\+Buffer}}
\item 
volatile uint8\+\_\+t \mbox{\hyperlink{main_8c_afa16784b155ba429ef87337ffe4c8ef2}{IMU\+\_\+rdy\+\_\+flag}} = 0
\item 
volatile uint8\+\_\+t \mbox{\hyperlink{main_8c_aae01ced9358c32bbda093e7d210a62cb}{LED\+\_\+rdy\+\_\+flag}} = 0
\item 
volatile uint8\+\_\+t \mbox{\hyperlink{main_8c_a81fff9d8317019d7b8b09b4221f16279}{CTRL\+\_\+rdy\+\_\+flag}} = 0
\item 
volatile float \mbox{\hyperlink{main_8c_a8e7dfdc468098a5f8415ff14d8f24c61}{real\+\_\+pos}} = 0
\item 
volatile float \mbox{\hyperlink{main_8c_ac360703ec72b1bae53031421664e4bef}{sys\+\_\+vel}} = 0
\end{DoxyCompactItemize}

\doxysubsection{Detailed Description}
Main program body. 

\begin{DoxyAttention}{Attention}

\end{DoxyAttention}
Copyright (c) 2024 STMicroelectronics. All rights reserved.

This software is licensed under terms that can be found in the LICENSE file in the root directory of this software component. If no LICENSE file comes with this software, it is provided AS-\/\+IS. 

\doxysubsection{Function Documentation}
\Hypertarget{main_8c_a1730ffe1e560465665eb47d9264826f9}\index{main.c@{main.c}!Error\_Handler@{Error\_Handler}}
\index{Error\_Handler@{Error\_Handler}!main.c@{main.c}}
\doxysubsubsection{\texorpdfstring{Error\_Handler()}{Error\_Handler()}}
{\footnotesize\ttfamily \label{main_8c_a1730ffe1e560465665eb47d9264826f9} 
void Error\+\_\+\+Handler (\begin{DoxyParamCaption}\item[{void}]{}{}\end{DoxyParamCaption})}

This function is executed in case of error occurrence. 

\begin{DoxyRetVals}{Return values}
{\em None} & \\
\hline
\end{DoxyRetVals}
\Hypertarget{main_8c_a8a3b0ad512a6e6c6157440b68d395eac}\index{main.c@{main.c}!HAL\_TIM\_PeriodElapsedCallback@{HAL\_TIM\_PeriodElapsedCallback}}
\index{HAL\_TIM\_PeriodElapsedCallback@{HAL\_TIM\_PeriodElapsedCallback}!main.c@{main.c}}
\doxysubsubsection{\texorpdfstring{HAL\_TIM\_PeriodElapsedCallback()}{HAL\_TIM\_PeriodElapsedCallback()}}
{\footnotesize\ttfamily \label{main_8c_a8a3b0ad512a6e6c6157440b68d395eac} 
void HAL\+\_\+\+TIM\+\_\+\+Period\+Elapsed\+Callback (\begin{DoxyParamCaption}\item[{TIM\+\_\+\+Handle\+Type\+Def \texorpdfstring{$\ast$}{*}}]{htim}{}\end{DoxyParamCaption})}

\Hypertarget{main_8c_ae494a9643f29b87d6d81e5264e60e57b}\index{main.c@{main.c}!HAL\_UART\_RxCpltCallback@{HAL\_UART\_RxCpltCallback}}
\index{HAL\_UART\_RxCpltCallback@{HAL\_UART\_RxCpltCallback}!main.c@{main.c}}
\doxysubsubsection{\texorpdfstring{HAL\_UART\_RxCpltCallback()}{HAL\_UART\_RxCpltCallback()}}
{\footnotesize\ttfamily \label{main_8c_ae494a9643f29b87d6d81e5264e60e57b} 
void HAL\+\_\+\+UART\+\_\+\+Rx\+Cplt\+Callback (\begin{DoxyParamCaption}\item[{UART\+\_\+\+Handle\+Type\+Def \texorpdfstring{$\ast$}{*}}]{huart}{}\end{DoxyParamCaption})}

\Hypertarget{main_8c_a840291bc02cba5474a4cb46a9b9566fe}\index{main.c@{main.c}!main@{main}}
\index{main@{main}!main.c@{main.c}}
\doxysubsubsection{\texorpdfstring{main()}{main()}}
{\footnotesize\ttfamily \label{main_8c_a840291bc02cba5474a4cb46a9b9566fe} 
int main (\begin{DoxyParamCaption}\item[{void}]{}{}\end{DoxyParamCaption})}

The application entry point. 

\begin{DoxyRetVals}{Return values}
{\em int} & \\
\hline
\end{DoxyRetVals}
\Hypertarget{main_8c_a70af21c671abfcc773614a9a4f63d920}\index{main.c@{main.c}!SystemClock\_Config@{SystemClock\_Config}}
\index{SystemClock\_Config@{SystemClock\_Config}!main.c@{main.c}}
\doxysubsubsection{\texorpdfstring{SystemClock\_Config()}{SystemClock\_Config()}}
{\footnotesize\ttfamily \label{main_8c_a70af21c671abfcc773614a9a4f63d920} 
void System\+Clock\+\_\+\+Config (\begin{DoxyParamCaption}\item[{void}]{}{}\end{DoxyParamCaption})}

System Clock Configuration. 

\begin{DoxyRetVals}{Return values}
{\em None} & \\
\hline
\end{DoxyRetVals}
Configure the main internal regulator output voltage

Initializes the RCC Oscillators according to the specified parameters in the RCC\+\_\+\+Osc\+Init\+Type\+Def structure.

Initializes the CPU, AHB and APB buses clocks

\doxysubsection{Variable Documentation}
\Hypertarget{main_8c_a81fff9d8317019d7b8b09b4221f16279}\index{main.c@{main.c}!CTRL\_rdy\_flag@{CTRL\_rdy\_flag}}
\index{CTRL\_rdy\_flag@{CTRL\_rdy\_flag}!main.c@{main.c}}
\doxysubsubsection{\texorpdfstring{CTRL\_rdy\_flag}{CTRL\_rdy\_flag}}
{\footnotesize\ttfamily \label{main_8c_a81fff9d8317019d7b8b09b4221f16279} 
volatile uint8\+\_\+t CTRL\+\_\+rdy\+\_\+flag = 0}

\Hypertarget{main_8c_af7b2c26e44dadaaa798a5c3d82914ba7}\index{main.c@{main.c}!hi2c1@{hi2c1}}
\index{hi2c1@{hi2c1}!main.c@{main.c}}
\doxysubsubsection{\texorpdfstring{hi2c1}{hi2c1}}
{\footnotesize\ttfamily \label{main_8c_af7b2c26e44dadaaa798a5c3d82914ba7} 
I2\+C\+\_\+\+Handle\+Type\+Def hi2c1}

\Hypertarget{main_8c_a25fc663547539bc49fecc0011bd76ab5}\index{main.c@{main.c}!htim1@{htim1}}
\index{htim1@{htim1}!main.c@{main.c}}
\doxysubsubsection{\texorpdfstring{htim1}{htim1}}
{\footnotesize\ttfamily \label{main_8c_a25fc663547539bc49fecc0011bd76ab5} 
TIM\+\_\+\+Handle\+Type\+Def htim1}

\Hypertarget{main_8c_a2f22f985c4f33318fdcd4cc996623bf4}\index{main.c@{main.c}!htim11@{htim11}}
\index{htim11@{htim11}!main.c@{main.c}}
\doxysubsubsection{\texorpdfstring{htim11}{htim11}}
{\footnotesize\ttfamily \label{main_8c_a2f22f985c4f33318fdcd4cc996623bf4} 
TIM\+\_\+\+Handle\+Type\+Def htim11}

\Hypertarget{main_8c_aac3d2c59ee0e3bbae1b99529a154eb62}\index{main.c@{main.c}!htim3@{htim3}}
\index{htim3@{htim3}!main.c@{main.c}}
\doxysubsubsection{\texorpdfstring{htim3}{htim3}}
{\footnotesize\ttfamily \label{main_8c_aac3d2c59ee0e3bbae1b99529a154eb62} 
TIM\+\_\+\+Handle\+Type\+Def htim3}

\Hypertarget{main_8c_a85788cec5a97ee377e4ee2e74f026484}\index{main.c@{main.c}!htim4@{htim4}}
\index{htim4@{htim4}!main.c@{main.c}}
\doxysubsubsection{\texorpdfstring{htim4}{htim4}}
{\footnotesize\ttfamily \label{main_8c_a85788cec5a97ee377e4ee2e74f026484} 
TIM\+\_\+\+Handle\+Type\+Def htim4}

\Hypertarget{main_8c_acefaeaaa3856ddddae7083b2d220fe4b}\index{main.c@{main.c}!htim5@{htim5}}
\index{htim5@{htim5}!main.c@{main.c}}
\doxysubsubsection{\texorpdfstring{htim5}{htim5}}
{\footnotesize\ttfamily \label{main_8c_acefaeaaa3856ddddae7083b2d220fe4b} 
TIM\+\_\+\+Handle\+Type\+Def htim5}

\Hypertarget{main_8c_aa9479c261d65eecedd3d9582f7f0f89c}\index{main.c@{main.c}!huart2@{huart2}}
\index{huart2@{huart2}!main.c@{main.c}}
\doxysubsubsection{\texorpdfstring{huart2}{huart2}}
{\footnotesize\ttfamily \label{main_8c_aa9479c261d65eecedd3d9582f7f0f89c} 
UART\+\_\+\+Handle\+Type\+Def huart2}

\Hypertarget{main_8c_a38905dda1d2fbff006c69db48eddba9d}\index{main.c@{main.c}!huart6@{huart6}}
\index{huart6@{huart6}!main.c@{main.c}}
\doxysubsubsection{\texorpdfstring{huart6}{huart6}}
{\footnotesize\ttfamily \label{main_8c_a38905dda1d2fbff006c69db48eddba9d} 
UART\+\_\+\+Handle\+Type\+Def huart6}

\Hypertarget{main_8c_a7c7b65fcf7197ae90670cd87ae675e95}\index{main.c@{main.c}!IMU@{IMU}}
\index{IMU@{IMU}!main.c@{main.c}}
\doxysubsubsection{\texorpdfstring{IMU}{IMU}}
{\footnotesize\ttfamily \label{main_8c_a7c7b65fcf7197ae90670cd87ae675e95} 
\mbox{\hyperlink{struct_i_c_m__20948}{ICM\+\_\+20948}} IMU}

{\bfseries Initial value\+:}
\begin{DoxyCode}{0}
\DoxyCodeLine{=\{}
\DoxyCodeLine{\ \ \ \ \ \ \ \ .hi2c\ =\ \&\mbox{\hyperlink{main_8c_af7b2c26e44dadaaa798a5c3d82914ba7}{hi2c1}},}
\DoxyCodeLine{\ \ \ \ \ \ \ \ .huart\ =\ \&\mbox{\hyperlink{main_8c_aa9479c261d65eecedd3d9582f7f0f89c}{huart2}}\ }
\DoxyCodeLine{\}}

\end{DoxyCode}
\Hypertarget{main_8c_afa16784b155ba429ef87337ffe4c8ef2}\index{main.c@{main.c}!IMU\_rdy\_flag@{IMU\_rdy\_flag}}
\index{IMU\_rdy\_flag@{IMU\_rdy\_flag}!main.c@{main.c}}
\doxysubsubsection{\texorpdfstring{IMU\_rdy\_flag}{IMU\_rdy\_flag}}
{\footnotesize\ttfamily \label{main_8c_afa16784b155ba429ef87337ffe4c8ef2} 
volatile uint8\+\_\+t IMU\+\_\+rdy\+\_\+flag = 0}

\Hypertarget{main_8c_a83ba99daa490dd49340550bb6fe885ba}\index{main.c@{main.c}!laptop@{laptop}}
\index{laptop@{laptop}!main.c@{main.c}}
\doxysubsubsection{\texorpdfstring{laptop}{laptop}}
{\footnotesize\ttfamily \label{main_8c_a83ba99daa490dd49340550bb6fe885ba} 
\mbox{\hyperlink{structodrive__t}{odrive\+\_\+t}} laptop}

{\bfseries Initial value\+:}
\begin{DoxyCode}{0}
\DoxyCodeLine{=\ \{}
\DoxyCodeLine{\ \ \ \ \ \ \ \ \ \ .huart\ =\ \&\mbox{\hyperlink{main_8c_aa9479c261d65eecedd3d9582f7f0f89c}{huart2}}}
\DoxyCodeLine{\}}

\end{DoxyCode}
\Hypertarget{main_8c_aae01ced9358c32bbda093e7d210a62cb}\index{main.c@{main.c}!LED\_rdy\_flag@{LED\_rdy\_flag}}
\index{LED\_rdy\_flag@{LED\_rdy\_flag}!main.c@{main.c}}
\doxysubsubsection{\texorpdfstring{LED\_rdy\_flag}{LED\_rdy\_flag}}
{\footnotesize\ttfamily \label{main_8c_aae01ced9358c32bbda093e7d210a62cb} 
volatile uint8\+\_\+t LED\+\_\+rdy\+\_\+flag = 0}

\Hypertarget{main_8c_ad04fe84a2d499fe57651a80bf68f29de}\index{main.c@{main.c}!odrive@{odrive}}
\index{odrive@{odrive}!main.c@{main.c}}
\doxysubsubsection{\texorpdfstring{odrive}{odrive}}
{\footnotesize\ttfamily \label{main_8c_ad04fe84a2d499fe57651a80bf68f29de} 
\mbox{\hyperlink{structodrive__t}{odrive\+\_\+t}} odrive}

{\bfseries Initial value\+:}
\begin{DoxyCode}{0}
\DoxyCodeLine{=\ \{}
\DoxyCodeLine{\ \ \ \ \ \ \ \ \ \ .huart\ =\ \&\mbox{\hyperlink{main_8c_a38905dda1d2fbff006c69db48eddba9d}{huart6}}}
\DoxyCodeLine{\}}

\end{DoxyCode}
\Hypertarget{main_8c_a8e7dfdc468098a5f8415ff14d8f24c61}\index{main.c@{main.c}!real\_pos@{real\_pos}}
\index{real\_pos@{real\_pos}!main.c@{main.c}}
\doxysubsubsection{\texorpdfstring{real\_pos}{real\_pos}}
{\footnotesize\ttfamily \label{main_8c_a8e7dfdc468098a5f8415ff14d8f24c61} 
volatile float real\+\_\+pos = 0}

\Hypertarget{main_8c_a076a5923dcfdcf95d91a8e24981ba4ee}\index{main.c@{main.c}!receivedData@{receivedData}}
\index{receivedData@{receivedData}!main.c@{main.c}}
\doxysubsubsection{\texorpdfstring{receivedData}{receivedData}}
{\footnotesize\ttfamily \label{main_8c_a076a5923dcfdcf95d91a8e24981ba4ee} 
uint8\+\_\+t received\+Data\hspace{0.3cm}{\ttfamily [extern]}}

\Hypertarget{main_8c_a20bc908e26cf958e1df3790d425cdb40}\index{main.c@{main.c}!responseFinishedFlag@{responseFinishedFlag}}
\index{responseFinishedFlag@{responseFinishedFlag}!main.c@{main.c}}
\doxysubsubsection{\texorpdfstring{responseFinishedFlag}{responseFinishedFlag}}
{\footnotesize\ttfamily \label{main_8c_a20bc908e26cf958e1df3790d425cdb40} 
uint8\+\_\+t response\+Finished\+Flag\hspace{0.3cm}{\ttfamily [extern]}}

\Hypertarget{main_8c_ad7394d71a5b03e693a17bc6ea557b4d9}\index{main.c@{main.c}!rxBuffer@{rxBuffer}}
\index{rxBuffer@{rxBuffer}!main.c@{main.c}}
\doxysubsubsection{\texorpdfstring{rxBuffer}{rxBuffer}}
{\footnotesize\ttfamily \label{main_8c_ad7394d71a5b03e693a17bc6ea557b4d9} 
uint8\+\_\+t rx\+Buffer\hspace{0.3cm}{\ttfamily [extern]}}

\Hypertarget{main_8c_a5f39e47fdf46ecf4822ca9875f6aacf3}\index{main.c@{main.c}!rxIndex@{rxIndex}}
\index{rxIndex@{rxIndex}!main.c@{main.c}}
\doxysubsubsection{\texorpdfstring{rxIndex}{rxIndex}}
{\footnotesize\ttfamily \label{main_8c_a5f39e47fdf46ecf4822ca9875f6aacf3} 
uint8\+\_\+t rx\+Index\hspace{0.3cm}{\ttfamily [extern]}}

\Hypertarget{main_8c_ac360703ec72b1bae53031421664e4bef}\index{main.c@{main.c}!sys\_vel@{sys\_vel}}
\index{sys\_vel@{sys\_vel}!main.c@{main.c}}
\doxysubsubsection{\texorpdfstring{sys\_vel}{sys\_vel}}
{\footnotesize\ttfamily \label{main_8c_ac360703ec72b1bae53031421664e4bef} 
volatile float sys\+\_\+vel = 0}

\Hypertarget{main_8c_af4d22e2e3395f74933e838aa8134e4a3}\index{main.c@{main.c}!transmitBuffer@{transmitBuffer}}
\index{transmitBuffer@{transmitBuffer}!main.c@{main.c}}
\doxysubsubsection{\texorpdfstring{transmitBuffer}{transmitBuffer}}
{\footnotesize\ttfamily \label{main_8c_af4d22e2e3395f74933e838aa8134e4a3} 
char transmit\+Buffer\hspace{0.3cm}{\ttfamily [extern]}}

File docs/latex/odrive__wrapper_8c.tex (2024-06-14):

\doxysection{odrive\+\_\+wrapper.\+c File Reference}
\hypertarget{odrive__wrapper_8c}{}\label{odrive__wrapper_8c}\index{odrive\_wrapper.c@{odrive\_wrapper.c}}

Provides functions for interfacing with an external ODrive controller.  

{\ttfamily \#include "{}main.\+h"{}}\newline
{\ttfamily \#include "{}odrive\+\_\+wrapper.\+h"{}}\newline
Include dependency graph for odrive\+\_\+wrapper.\+c\+:\nopagebreak
\begin{figure}[H]
\begin{center}
\leavevmode

\end{center}
\end{figure}
\doxysubsubsection*{Functions}
\begin{DoxyCompactItemize}
\item 
void \mbox{\hyperlink{odrive__wrapper_8c_a25d657b24b80292f58a570b02e7aa428}{ODRIVE\+\_\+\+Reboot}} (\mbox{\hyperlink{structodrive__t}{odrive\+\_\+t}} \texorpdfstring{$\ast$}{*}p)
\begin{DoxyCompactList}\small\item\em Sends ASCII command to reboot ODrive. \end{DoxyCompactList}\item 
void \mbox{\hyperlink{odrive__wrapper_8c_ab13b958603fb943556b9a7c32fc95bac}{ODRIVE\+\_\+\+Clear\+Errors}} (\mbox{\hyperlink{structodrive__t}{odrive\+\_\+t}} \texorpdfstring{$\ast$}{*}p)
\begin{DoxyCompactList}\small\item\em Sends ASCII command to clear errors on ODrive. \end{DoxyCompactList}\item 
void \mbox{\hyperlink{odrive__wrapper_8c_a7b3454ebe0e4fdd3a2a0dc64f72719c9}{ODRIVE\+\_\+\+Set\+Position}} (\mbox{\hyperlink{structodrive__t}{odrive\+\_\+t}} \texorpdfstring{$\ast$}{*}p, int motor\+\_\+number, float position, float velocity\+\_\+lim, float torque\+\_\+lim)
\begin{DoxyCompactList}\small\item\em Sends ASCII command to send position setpoint to ODrive. \end{DoxyCompactList}\item 
void \mbox{\hyperlink{odrive__wrapper_8c_a18367d959b193c49f6c7534cc7ab857f}{ODRIVE\+\_\+\+Set\+Position\+FF}} (\mbox{\hyperlink{structodrive__t}{odrive\+\_\+t}} \texorpdfstring{$\ast$}{*}p, int motor\+\_\+number, float position, float velocity\+\_\+feedforward, float current\+\_\+feedforward)
\begin{DoxyCompactList}\small\item\em Sends ASCII command to send position setpoint with feedforward ODrive. \end{DoxyCompactList}\item 
void \mbox{\hyperlink{odrive__wrapper_8c_a896ffd1031a488a9f22fd92ff20bd384}{ODRIVE\+\_\+\+Set\+Velocity}} (\mbox{\hyperlink{structodrive__t}{odrive\+\_\+t}} \texorpdfstring{$\ast$}{*}p, int motor\+\_\+number, float velocity)
\begin{DoxyCompactList}\small\item\em Sends ASCII command to send velocity setpoint to ODrive. \end{DoxyCompactList}\item 
void \mbox{\hyperlink{odrive__wrapper_8c_a6fff222e9c4e938392faacf4cccd1925}{ODRIVE\+\_\+\+Set\+Torque}} (\mbox{\hyperlink{structodrive__t}{odrive\+\_\+t}} \texorpdfstring{$\ast$}{*}p, int motor\+\_\+number, float torque)
\begin{DoxyCompactList}\small\item\em Sends ASCII command to send torque setpoint to ODrive. \end{DoxyCompactList}\item 
uint8\+\_\+t \texorpdfstring{$\ast$}{*} \mbox{\hyperlink{odrive__wrapper_8c_a42dae01f885677084b5223cb8a259b66}{ODRIVE\+\_\+\+Get\+Feedback}} (\mbox{\hyperlink{structodrive__t}{odrive\+\_\+t}} \texorpdfstring{$\ast$}{*}p, int motor\+\_\+number)
\begin{DoxyCompactList}\small\item\em Sends ASCII command to get current position and velocity from ODrive. \end{DoxyCompactList}\item 
uint8\+\_\+t \texorpdfstring{$\ast$}{*} \mbox{\hyperlink{odrive__wrapper_8c_a60cc06522e5b60f0383052c1f9cea4c5}{ODRIVE\+\_\+\+Get\+VBus}} (\mbox{\hyperlink{structodrive__t}{odrive\+\_\+t}} \texorpdfstring{$\ast$}{*}p)
\begin{DoxyCompactList}\small\item\em Sends ASCII command to get VBUS voltage from ODrive. \end{DoxyCompactList}\item 
uint8\+\_\+t \texorpdfstring{$\ast$}{*} \mbox{\hyperlink{odrive__wrapper_8c_aac7f31794321642f9aa5064b454f4799}{ODRIVE\+\_\+\+Is\+Calibrated}} (\mbox{\hyperlink{structodrive__t}{odrive\+\_\+t}} \texorpdfstring{$\ast$}{*}p)
\begin{DoxyCompactList}\small\item\em Sends ASCII command to check calibrated status ODrive. \end{DoxyCompactList}\item 
void \mbox{\hyperlink{odrive__wrapper_8c_a6ea52cd425986e041299100c9ce37564}{ODRIVE\+\_\+\+Write\+Param}} (\mbox{\hyperlink{structodrive__t}{odrive\+\_\+t}} \texorpdfstring{$\ast$}{*}p, char param\mbox{[}$\,$\mbox{]})
\begin{DoxyCompactList}\small\item\em Sends ASCII command to ODrive. \end{DoxyCompactList}\item 
uint8\+\_\+t \texorpdfstring{$\ast$}{*} \mbox{\hyperlink{odrive__wrapper_8c_ad14c9d5698a70cc0796f76190bdd1aa8}{ODRIVE\+\_\+\+Read\+Param}} (\mbox{\hyperlink{structodrive__t}{odrive\+\_\+t}} \texorpdfstring{$\ast$}{*}p, char param\mbox{[}$\,$\mbox{]})
\begin{DoxyCompactList}\small\item\em Receives ASCII command from ODrive. \end{DoxyCompactList}\item 
uint8\+\_\+t \texorpdfstring{$\ast$}{*} \mbox{\hyperlink{odrive__wrapper_8c_a88ecdd0331d179bc1dbe55975976a190}{get\+Received\+String}} (\mbox{\hyperlink{structodrive__t}{odrive\+\_\+t}} \texorpdfstring{$\ast$}{*}p)
\begin{DoxyCompactList}\small\item\em Sends ASCII command to reboot ODrive. \end{DoxyCompactList}\item 
void \mbox{\hyperlink{odrive__wrapper_8c_ab6435b6238a1cb4ff3627f8736a86d72}{start\+\_\+receive\+\_\+string}} (\mbox{\hyperlink{structodrive__t}{odrive\+\_\+t}} \texorpdfstring{$\ast$}{*}p)
\begin{DoxyCompactList}\small\item\em Starts receiving a new string via UART. \end{DoxyCompactList}\item 
void \mbox{\hyperlink{odrive__wrapper_8c_a38cf8e45ebb6bf5c5afcfde2e0df6a89}{ODRIVE\+\_\+\+Receive\+\_\+\+Callback}} (UART\+\_\+\+Handle\+Type\+Def \texorpdfstring{$\ast$}{*}huart, \mbox{\hyperlink{structodrive__t}{odrive\+\_\+t}} \texorpdfstring{$\ast$}{*}p)
\begin{DoxyCompactList}\small\item\em Callback to properly receive strings via UART. \end{DoxyCompactList}\item 
void \mbox{\hyperlink{odrive__wrapper_8c_a4e1fce1b7c1fe420d4139acbc11712dd}{extract\+Floats}} (uint8\+\_\+t \texorpdfstring{$\ast$}{*}message, float \texorpdfstring{$\ast$}{*}\mbox{\hyperlink{controller_8c_ad50f9053a1bfede86c60be067d744d71}{x}}, float \texorpdfstring{$\ast$}{*}y)
\begin{DoxyCompactList}\small\item\em Extracts floats from a given string of two floats in ASCII protocol format. \end{DoxyCompactList}\end{DoxyCompactItemize}
\doxysubsubsection*{Variables}
\begin{DoxyCompactItemize}
\item 
uint8\+\_\+t \mbox{\hyperlink{odrive__wrapper_8c_af59853d08dfd3128856dea473e04b8ab}{rx\+Buffer}} \mbox{[}\mbox{\hyperlink{odrive__wrapper_8h_a6b20d41d6252e9871430c242cb1a56e7}{BUFFER\+\_\+\+SIZE}}\mbox{]}
\item 
uint8\+\_\+t \mbox{\hyperlink{odrive__wrapper_8c_a5f39e47fdf46ecf4822ca9875f6aacf3}{rx\+Index}} = 0
\item 
uint8\+\_\+t \mbox{\hyperlink{odrive__wrapper_8c_a20bc908e26cf958e1df3790d425cdb40}{response\+Finished\+Flag}} = 0
\item 
uint8\+\_\+t \mbox{\hyperlink{odrive__wrapper_8c_afb5471a16c58930c1a97e82caeb880b2}{received\+Data}} \mbox{[}\mbox{\hyperlink{odrive__wrapper_8h_a6b20d41d6252e9871430c242cb1a56e7}{BUFFER\+\_\+\+SIZE}}\mbox{]}
\end{DoxyCompactItemize}

\doxysubsection{Detailed Description}
Provides functions for interfacing with an external ODrive controller. 

Implements the ASCII protocol as defined by ODrive\+: \href{https://docs.odriverobotics.com/v/latest/manual/ascii-protocol.html}{\texttt{ https\+://docs.\+odriverobotics.\+com/v/latest/manual/ascii-\/protocol.\+html}} 

\doxysubsection{Function Documentation}
\Hypertarget{odrive__wrapper_8c_a4e1fce1b7c1fe420d4139acbc11712dd}\index{odrive\_wrapper.c@{odrive\_wrapper.c}!extractFloats@{extractFloats}}
\index{extractFloats@{extractFloats}!odrive\_wrapper.c@{odrive\_wrapper.c}}
\doxysubsubsection{\texorpdfstring{extractFloats()}{extractFloats()}}
{\footnotesize\ttfamily \label{odrive__wrapper_8c_a4e1fce1b7c1fe420d4139acbc11712dd} 
void extract\+Floats (\begin{DoxyParamCaption}\item[{uint8\+\_\+t \texorpdfstring{$\ast$}{*}}]{message}{, }\item[{float \texorpdfstring{$\ast$}{*}}]{x}{, }\item[{float \texorpdfstring{$\ast$}{*}}]{y}{}\end{DoxyParamCaption})}

Extracts floats from a given string of two floats in ASCII protocol format. 

For use in converting feedback message. 
\begin{DoxyParams}{Parameters}
{\em message} & Pointer to the received message. \\
\hline
{\em x} & Pointer to a first float. \\
\hline
{\em y} & Pointer to a second float. \\
\hline
\end{DoxyParams}
\Hypertarget{odrive__wrapper_8c_a88ecdd0331d179bc1dbe55975976a190}\index{odrive\_wrapper.c@{odrive\_wrapper.c}!getReceivedString@{getReceivedString}}
\index{getReceivedString@{getReceivedString}!odrive\_wrapper.c@{odrive\_wrapper.c}}
\doxysubsubsection{\texorpdfstring{getReceivedString()}{getReceivedString()}}
{\footnotesize\ttfamily \label{odrive__wrapper_8c_a88ecdd0331d179bc1dbe55975976a190} 
uint8\+\_\+t \texorpdfstring{$\ast$}{*} get\+Received\+String (\begin{DoxyParamCaption}\item[{\mbox{\hyperlink{structodrive__t}{odrive\+\_\+t}} \texorpdfstring{$\ast$}{*}}]{p}{}\end{DoxyParamCaption})}

Sends ASCII command to reboot ODrive. 

\begin{DoxyParams}{Parameters}
{\em p} & Pointer to an ODrive object. \\
\hline
\end{DoxyParams}
\Hypertarget{odrive__wrapper_8c_ab13b958603fb943556b9a7c32fc95bac}\index{odrive\_wrapper.c@{odrive\_wrapper.c}!ODRIVE\_ClearErrors@{ODRIVE\_ClearErrors}}
\index{ODRIVE\_ClearErrors@{ODRIVE\_ClearErrors}!odrive\_wrapper.c@{odrive\_wrapper.c}}
\doxysubsubsection{\texorpdfstring{ODRIVE\_ClearErrors()}{ODRIVE\_ClearErrors()}}
{\footnotesize\ttfamily \label{odrive__wrapper_8c_ab13b958603fb943556b9a7c32fc95bac} 
void ODRIVE\+\_\+\+Clear\+Errors (\begin{DoxyParamCaption}\item[{\mbox{\hyperlink{structodrive__t}{odrive\+\_\+t}} \texorpdfstring{$\ast$}{*}}]{p}{}\end{DoxyParamCaption})}

Sends ASCII command to clear errors on ODrive. 

\begin{DoxyParams}{Parameters}
{\em p} & Pointer to an ODrive object. \\
\hline
\end{DoxyParams}
\Hypertarget{odrive__wrapper_8c_a42dae01f885677084b5223cb8a259b66}\index{odrive\_wrapper.c@{odrive\_wrapper.c}!ODRIVE\_GetFeedback@{ODRIVE\_GetFeedback}}
\index{ODRIVE\_GetFeedback@{ODRIVE\_GetFeedback}!odrive\_wrapper.c@{odrive\_wrapper.c}}
\doxysubsubsection{\texorpdfstring{ODRIVE\_GetFeedback()}{ODRIVE\_GetFeedback()}}
{\footnotesize\ttfamily \label{odrive__wrapper_8c_a42dae01f885677084b5223cb8a259b66} 
uint8\+\_\+t \texorpdfstring{$\ast$}{*} ODRIVE\+\_\+\+Get\+Feedback (\begin{DoxyParamCaption}\item[{\mbox{\hyperlink{structodrive__t}{odrive\+\_\+t}} \texorpdfstring{$\ast$}{*}}]{p}{, }\item[{int}]{motor\+\_\+number}{}\end{DoxyParamCaption})}

Sends ASCII command to get current position and velocity from ODrive. 

\begin{DoxyParams}{Parameters}
{\em p} & Pointer to an ODrive object. \\
\hline
{\em motor\+\_\+number} & Motor number on ODrive. Typically 0. \\
\hline
\end{DoxyParams}
\Hypertarget{odrive__wrapper_8c_a60cc06522e5b60f0383052c1f9cea4c5}\index{odrive\_wrapper.c@{odrive\_wrapper.c}!ODRIVE\_GetVBus@{ODRIVE\_GetVBus}}
\index{ODRIVE\_GetVBus@{ODRIVE\_GetVBus}!odrive\_wrapper.c@{odrive\_wrapper.c}}
\doxysubsubsection{\texorpdfstring{ODRIVE\_GetVBus()}{ODRIVE\_GetVBus()}}
{\footnotesize\ttfamily \label{odrive__wrapper_8c_a60cc06522e5b60f0383052c1f9cea4c5} 
uint8\+\_\+t \texorpdfstring{$\ast$}{*} ODRIVE\+\_\+\+Get\+VBus (\begin{DoxyParamCaption}\item[{\mbox{\hyperlink{structodrive__t}{odrive\+\_\+t}} \texorpdfstring{$\ast$}{*}}]{p}{}\end{DoxyParamCaption})}

Sends ASCII command to get VBUS voltage from ODrive. 

Used mainly as a test to see if we can send and receive UART commands. 
\begin{DoxyParams}{Parameters}
{\em p} & Pointer to an ODrive object. \\
\hline
\end{DoxyParams}
\Hypertarget{odrive__wrapper_8c_aac7f31794321642f9aa5064b454f4799}\index{odrive\_wrapper.c@{odrive\_wrapper.c}!ODRIVE\_IsCalibrated@{ODRIVE\_IsCalibrated}}
\index{ODRIVE\_IsCalibrated@{ODRIVE\_IsCalibrated}!odrive\_wrapper.c@{odrive\_wrapper.c}}
\doxysubsubsection{\texorpdfstring{ODRIVE\_IsCalibrated()}{ODRIVE\_IsCalibrated()}}
{\footnotesize\ttfamily \label{odrive__wrapper_8c_aac7f31794321642f9aa5064b454f4799} 
uint8\+\_\+t \texorpdfstring{$\ast$}{*} ODRIVE\+\_\+\+Is\+Calibrated (\begin{DoxyParamCaption}\item[{\mbox{\hyperlink{structodrive__t}{odrive\+\_\+t}} \texorpdfstring{$\ast$}{*}}]{p}{}\end{DoxyParamCaption})}

Sends ASCII command to check calibrated status ODrive. 

I think this one is broken. 
\begin{DoxyParams}{Parameters}
{\em p} & Pointer to an ODrive object. \\
\hline
\end{DoxyParams}
\Hypertarget{odrive__wrapper_8c_ad14c9d5698a70cc0796f76190bdd1aa8}\index{odrive\_wrapper.c@{odrive\_wrapper.c}!ODRIVE\_ReadParam@{ODRIVE\_ReadParam}}
\index{ODRIVE\_ReadParam@{ODRIVE\_ReadParam}!odrive\_wrapper.c@{odrive\_wrapper.c}}
\doxysubsubsection{\texorpdfstring{ODRIVE\_ReadParam()}{ODRIVE\_ReadParam()}}
{\footnotesize\ttfamily \label{odrive__wrapper_8c_ad14c9d5698a70cc0796f76190bdd1aa8} 
uint8\+\_\+t \texorpdfstring{$\ast$}{*} ODRIVE\+\_\+\+Read\+Param (\begin{DoxyParamCaption}\item[{\mbox{\hyperlink{structodrive__t}{odrive\+\_\+t}} \texorpdfstring{$\ast$}{*}}]{p}{, }\item[{char}]{param}{\mbox{[}$\,$\mbox{]}}\end{DoxyParamCaption})}

Receives ASCII command from ODrive. 

\begin{DoxyParams}{Parameters}
{\em p} & Pointer to an ODrive object. \\
\hline
{\em param\mbox{[}$\,$\mbox{]}} & Parameter to read from, in string format. \\
\hline
\end{DoxyParams}
\Hypertarget{odrive__wrapper_8c_a25d657b24b80292f58a570b02e7aa428}\index{odrive\_wrapper.c@{odrive\_wrapper.c}!ODRIVE\_Reboot@{ODRIVE\_Reboot}}
\index{ODRIVE\_Reboot@{ODRIVE\_Reboot}!odrive\_wrapper.c@{odrive\_wrapper.c}}
\doxysubsubsection{\texorpdfstring{ODRIVE\_Reboot()}{ODRIVE\_Reboot()}}
{\footnotesize\ttfamily \label{odrive__wrapper_8c_a25d657b24b80292f58a570b02e7aa428} 
void ODRIVE\+\_\+\+Reboot (\begin{DoxyParamCaption}\item[{\mbox{\hyperlink{structodrive__t}{odrive\+\_\+t}} \texorpdfstring{$\ast$}{*}}]{p}{}\end{DoxyParamCaption})}

Sends ASCII command to reboot ODrive. 

\begin{DoxyParams}{Parameters}
{\em p} & Pointer to an ODrive object. \\
\hline
\end{DoxyParams}
\Hypertarget{odrive__wrapper_8c_a38cf8e45ebb6bf5c5afcfde2e0df6a89}\index{odrive\_wrapper.c@{odrive\_wrapper.c}!ODRIVE\_Receive\_Callback@{ODRIVE\_Receive\_Callback}}
\index{ODRIVE\_Receive\_Callback@{ODRIVE\_Receive\_Callback}!odrive\_wrapper.c@{odrive\_wrapper.c}}
\doxysubsubsection{\texorpdfstring{ODRIVE\_Receive\_Callback()}{ODRIVE\_Receive\_Callback()}}
{\footnotesize\ttfamily \label{odrive__wrapper_8c_a38cf8e45ebb6bf5c5afcfde2e0df6a89} 
void ODRIVE\+\_\+\+Receive\+\_\+\+Callback (\begin{DoxyParamCaption}\item[{UART\+\_\+\+Handle\+Type\+Def \texorpdfstring{$\ast$}{*}}]{huart}{, }\item[{\mbox{\hyperlink{structodrive__t}{odrive\+\_\+t}} \texorpdfstring{$\ast$}{*}}]{p}{}\end{DoxyParamCaption})}

Callback to properly receive strings via UART. 

\begin{DoxyParams}{Parameters}
{\em p} & Pointer to an ODrive object. \\
\hline
{\em huart} & UART object that is compared to ODrive object to confirm they are the same. \\
\hline
\end{DoxyParams}
\Hypertarget{odrive__wrapper_8c_a7b3454ebe0e4fdd3a2a0dc64f72719c9}\index{odrive\_wrapper.c@{odrive\_wrapper.c}!ODRIVE\_SetPosition@{ODRIVE\_SetPosition}}
\index{ODRIVE\_SetPosition@{ODRIVE\_SetPosition}!odrive\_wrapper.c@{odrive\_wrapper.c}}
\doxysubsubsection{\texorpdfstring{ODRIVE\_SetPosition()}{ODRIVE\_SetPosition()}}
{\footnotesize\ttfamily \label{odrive__wrapper_8c_a7b3454ebe0e4fdd3a2a0dc64f72719c9} 
void ODRIVE\+\_\+\+Set\+Position (\begin{DoxyParamCaption}\item[{\mbox{\hyperlink{structodrive__t}{odrive\+\_\+t}} \texorpdfstring{$\ast$}{*}}]{p}{, }\item[{int}]{motor\+\_\+number}{, }\item[{float}]{position}{, }\item[{float}]{velocity\+\_\+lim}{, }\item[{float}]{torque\+\_\+lim}{}\end{DoxyParamCaption})}

Sends ASCII command to send position setpoint to ODrive. 

\begin{DoxyParams}{Parameters}
{\em p} & Pointer to an ODrive object. \\
\hline
{\em motor\+\_\+number} & Motor number on ODrive. Typically 0. \\
\hline
{\em position} & Position setpoint \\
\hline
{\em velocity\+\_\+lim} & Velocity limit \\
\hline
{\em torque\+\_\+lim} & Torque limit \\
\hline
\end{DoxyParams}
\Hypertarget{odrive__wrapper_8c_a18367d959b193c49f6c7534cc7ab857f}\index{odrive\_wrapper.c@{odrive\_wrapper.c}!ODRIVE\_SetPositionFF@{ODRIVE\_SetPositionFF}}
\index{ODRIVE\_SetPositionFF@{ODRIVE\_SetPositionFF}!odrive\_wrapper.c@{odrive\_wrapper.c}}
\doxysubsubsection{\texorpdfstring{ODRIVE\_SetPositionFF()}{ODRIVE\_SetPositionFF()}}
{\footnotesize\ttfamily \label{odrive__wrapper_8c_a18367d959b193c49f6c7534cc7ab857f} 
void ODRIVE\+\_\+\+Set\+Position\+FF (\begin{DoxyParamCaption}\item[{\mbox{\hyperlink{structodrive__t}{odrive\+\_\+t}} \texorpdfstring{$\ast$}{*}}]{p}{, }\item[{int}]{motor\+\_\+number}{, }\item[{float}]{position}{, }\item[{float}]{velocity\+\_\+feedforward}{, }\item[{float}]{current\+\_\+feedforward}{}\end{DoxyParamCaption})}

Sends ASCII command to send position setpoint with feedforward ODrive. 

\begin{DoxyParams}{Parameters}
{\em p} & Pointer to an ODrive object. \\
\hline
{\em motor\+\_\+number} & Motor number on ODrive. Typically 0. \\
\hline
{\em position} & Position setpoint \\
\hline
{\em velocity\+\_\+feedforward} & Velocity feedforward value. \\
\hline
{\em current\+\_\+feedforward} & Current feedforward value. \\
\hline
\end{DoxyParams}
\Hypertarget{odrive__wrapper_8c_a6fff222e9c4e938392faacf4cccd1925}\index{odrive\_wrapper.c@{odrive\_wrapper.c}!ODRIVE\_SetTorque@{ODRIVE\_SetTorque}}
\index{ODRIVE\_SetTorque@{ODRIVE\_SetTorque}!odrive\_wrapper.c@{odrive\_wrapper.c}}
\doxysubsubsection{\texorpdfstring{ODRIVE\_SetTorque()}{ODRIVE\_SetTorque()}}
{\footnotesize\ttfamily \label{odrive__wrapper_8c_a6fff222e9c4e938392faacf4cccd1925} 
void ODRIVE\+\_\+\+Set\+Torque (\begin{DoxyParamCaption}\item[{\mbox{\hyperlink{structodrive__t}{odrive\+\_\+t}} \texorpdfstring{$\ast$}{*}}]{p}{, }\item[{int}]{motor\+\_\+number}{, }\item[{float}]{torque}{}\end{DoxyParamCaption})}

Sends ASCII command to send torque setpoint to ODrive. 

\begin{DoxyParams}{Parameters}
{\em p} & Pointer to an ODrive object. \\
\hline
{\em motor\+\_\+number} & Motor number on ODrive. Typically 0. \\
\hline
{\em torque} & Torque setpoint. \\
\hline
\end{DoxyParams}
\Hypertarget{odrive__wrapper_8c_a896ffd1031a488a9f22fd92ff20bd384}\index{odrive\_wrapper.c@{odrive\_wrapper.c}!ODRIVE\_SetVelocity@{ODRIVE\_SetVelocity}}
\index{ODRIVE\_SetVelocity@{ODRIVE\_SetVelocity}!odrive\_wrapper.c@{odrive\_wrapper.c}}
\doxysubsubsection{\texorpdfstring{ODRIVE\_SetVelocity()}{ODRIVE\_SetVelocity()}}
{\footnotesize\ttfamily \label{odrive__wrapper_8c_a896ffd1031a488a9f22fd92ff20bd384} 
void ODRIVE\+\_\+\+Set\+Velocity (\begin{DoxyParamCaption}\item[{\mbox{\hyperlink{structodrive__t}{odrive\+\_\+t}} \texorpdfstring{$\ast$}{*}}]{p}{, }\item[{int}]{motor\+\_\+number}{, }\item[{float}]{velocity}{}\end{DoxyParamCaption})}

Sends ASCII command to send velocity setpoint to ODrive. 

\begin{DoxyParams}{Parameters}
{\em p} & Pointer to an ODrive object. \\
\hline
{\em motor\+\_\+number} & Motor number on ODrive. Typically 0. \\
\hline
{\em velocity} & Velocity setpoint. \\
\hline
\end{DoxyParams}
\Hypertarget{odrive__wrapper_8c_a6ea52cd425986e041299100c9ce37564}\index{odrive\_wrapper.c@{odrive\_wrapper.c}!ODRIVE\_WriteParam@{ODRIVE\_WriteParam}}
\index{ODRIVE\_WriteParam@{ODRIVE\_WriteParam}!odrive\_wrapper.c@{odrive\_wrapper.c}}
\doxysubsubsection{\texorpdfstring{ODRIVE\_WriteParam()}{ODRIVE\_WriteParam()}}
{\footnotesize\ttfamily \label{odrive__wrapper_8c_a6ea52cd425986e041299100c9ce37564} 
void ODRIVE\+\_\+\+Write\+Param (\begin{DoxyParamCaption}\item[{\mbox{\hyperlink{structodrive__t}{odrive\+\_\+t}} \texorpdfstring{$\ast$}{*}}]{p}{, }\item[{char}]{param}{\mbox{[}$\,$\mbox{]}}\end{DoxyParamCaption})}

Sends ASCII command to ODrive. 

\begin{DoxyParams}{Parameters}
{\em p} & Pointer to an ODrive object. \\
\hline
{\em param\mbox{[}$\,$\mbox{]}} & Parameter to write to, in string format. \\
\hline
\end{DoxyParams}
\Hypertarget{odrive__wrapper_8c_ab6435b6238a1cb4ff3627f8736a86d72}\index{odrive\_wrapper.c@{odrive\_wrapper.c}!start\_receive\_string@{start\_receive\_string}}
\index{start\_receive\_string@{start\_receive\_string}!odrive\_wrapper.c@{odrive\_wrapper.c}}
\doxysubsubsection{\texorpdfstring{start\_receive\_string()}{start\_receive\_string()}}
{\footnotesize\ttfamily \label{odrive__wrapper_8c_ab6435b6238a1cb4ff3627f8736a86d72} 
void start\+\_\+receive\+\_\+string (\begin{DoxyParamCaption}\item[{\mbox{\hyperlink{structodrive__t}{odrive\+\_\+t}} \texorpdfstring{$\ast$}{*}}]{p}{}\end{DoxyParamCaption})}

Starts receiving a new string via UART. 

Sets the buffer index to zero and sets up HAL\+\_\+\+UART\+\_\+\+Receive correctly for the ODrive object. 
\begin{DoxyParams}{Parameters}
{\em p} & Pointer to an ODrive object. \\
\hline
\end{DoxyParams}

\doxysubsection{Variable Documentation}
\Hypertarget{odrive__wrapper_8c_afb5471a16c58930c1a97e82caeb880b2}\index{odrive\_wrapper.c@{odrive\_wrapper.c}!receivedData@{receivedData}}
\index{receivedData@{receivedData}!odrive\_wrapper.c@{odrive\_wrapper.c}}
\doxysubsubsection{\texorpdfstring{receivedData}{receivedData}}
{\footnotesize\ttfamily \label{odrive__wrapper_8c_afb5471a16c58930c1a97e82caeb880b2} 
uint8\+\_\+t received\+Data\mbox{[}\mbox{\hyperlink{odrive__wrapper_8h_a6b20d41d6252e9871430c242cb1a56e7}{BUFFER\+\_\+\+SIZE}}\mbox{]}}

\Hypertarget{odrive__wrapper_8c_a20bc908e26cf958e1df3790d425cdb40}\index{odrive\_wrapper.c@{odrive\_wrapper.c}!responseFinishedFlag@{responseFinishedFlag}}
\index{responseFinishedFlag@{responseFinishedFlag}!odrive\_wrapper.c@{odrive\_wrapper.c}}
\doxysubsubsection{\texorpdfstring{responseFinishedFlag}{responseFinishedFlag}}
{\footnotesize\ttfamily \label{odrive__wrapper_8c_a20bc908e26cf958e1df3790d425cdb40} 
uint8\+\_\+t response\+Finished\+Flag = 0}

\Hypertarget{odrive__wrapper_8c_af59853d08dfd3128856dea473e04b8ab}\index{odrive\_wrapper.c@{odrive\_wrapper.c}!rxBuffer@{rxBuffer}}
\index{rxBuffer@{rxBuffer}!odrive\_wrapper.c@{odrive\_wrapper.c}}
\doxysubsubsection{\texorpdfstring{rxBuffer}{rxBuffer}}
{\footnotesize\ttfamily \label{odrive__wrapper_8c_af59853d08dfd3128856dea473e04b8ab} 
uint8\+\_\+t rx\+Buffer\mbox{[}\mbox{\hyperlink{odrive__wrapper_8h_a6b20d41d6252e9871430c242cb1a56e7}{BUFFER\+\_\+\+SIZE}}\mbox{]}}

\Hypertarget{odrive__wrapper_8c_a5f39e47fdf46ecf4822ca9875f6aacf3}\index{odrive\_wrapper.c@{odrive\_wrapper.c}!rxIndex@{rxIndex}}
\index{rxIndex@{rxIndex}!odrive\_wrapper.c@{odrive\_wrapper.c}}
\doxysubsubsection{\texorpdfstring{rxIndex}{rxIndex}}
{\footnotesize\ttfamily \label{odrive__wrapper_8c_a5f39e47fdf46ecf4822ca9875f6aacf3} 
uint8\+\_\+t rx\+Index = 0}

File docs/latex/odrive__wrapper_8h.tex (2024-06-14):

\doxysection{odrive\+\_\+wrapper.\+h File Reference}
\hypertarget{odrive__wrapper_8h}{}\label{odrive__wrapper_8h}\index{odrive\_wrapper.h@{odrive\_wrapper.h}}
{\ttfamily \#include "{}main.\+h"{}}\newline
Include dependency graph for odrive\+\_\+wrapper.\+h\+:\nopagebreak
\begin{figure}[H]
\begin{center}
\leavevmode
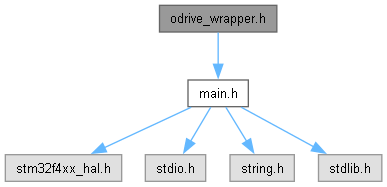
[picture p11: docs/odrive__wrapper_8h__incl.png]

\end{center}
\end{figure}
This graph shows which files directly or indirectly include this file\+:\nopagebreak
\begin{figure}[H]
\begin{center}
\leavevmode
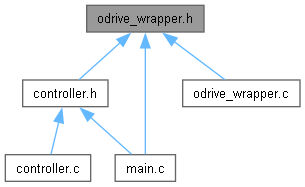
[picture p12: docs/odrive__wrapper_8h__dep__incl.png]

\end{center}
\end{figure}
\doxysubsubsection*{Data Structures}
\begin{DoxyCompactItemize}
\item 
struct \mbox{\hyperlink{structodrive__t}{odrive\+\_\+t}}
\end{DoxyCompactItemize}
\doxysubsubsection*{Macros}
\begin{DoxyCompactItemize}
\item 
\#define \mbox{\hyperlink{odrive__wrapper_8h_a6b20d41d6252e9871430c242cb1a56e7}{BUFFER\+\_\+\+SIZE}}~50
\end{DoxyCompactItemize}
\doxysubsubsection*{Functions}
\begin{DoxyCompactItemize}
\item 
void \mbox{\hyperlink{odrive__wrapper_8h_a25d657b24b80292f58a570b02e7aa428}{ODRIVE\+\_\+\+Reboot}} (\mbox{\hyperlink{structodrive__t}{odrive\+\_\+t}} \texorpdfstring{$\ast$}{*}p)
\begin{DoxyCompactList}\small\item\em Sends ASCII command to reboot ODrive. \end{DoxyCompactList}\item 
void \mbox{\hyperlink{odrive__wrapper_8h_ab13b958603fb943556b9a7c32fc95bac}{ODRIVE\+\_\+\+Clear\+Errors}} (\mbox{\hyperlink{structodrive__t}{odrive\+\_\+t}} \texorpdfstring{$\ast$}{*}p)
\begin{DoxyCompactList}\small\item\em Sends ASCII command to clear errors on ODrive. \end{DoxyCompactList}\item 
void \mbox{\hyperlink{odrive__wrapper_8h_a7b3454ebe0e4fdd3a2a0dc64f72719c9}{ODRIVE\+\_\+\+Set\+Position}} (\mbox{\hyperlink{structodrive__t}{odrive\+\_\+t}} \texorpdfstring{$\ast$}{*}p, int motor\+\_\+number, float position, float velocity\+\_\+lim, float torque\+\_\+lim)
\begin{DoxyCompactList}\small\item\em Sends ASCII command to send position setpoint to ODrive. \end{DoxyCompactList}\item 
void \mbox{\hyperlink{odrive__wrapper_8h_a18367d959b193c49f6c7534cc7ab857f}{ODRIVE\+\_\+\+Set\+Position\+FF}} (\mbox{\hyperlink{structodrive__t}{odrive\+\_\+t}} \texorpdfstring{$\ast$}{*}p, int motor\+\_\+number, float position, float velocity\+\_\+feedforward, float current\+\_\+feedforward)
\begin{DoxyCompactList}\small\item\em Sends ASCII command to send position setpoint with feedforward ODrive. \end{DoxyCompactList}\item 
void \mbox{\hyperlink{odrive__wrapper_8h_a896ffd1031a488a9f22fd92ff20bd384}{ODRIVE\+\_\+\+Set\+Velocity}} (\mbox{\hyperlink{structodrive__t}{odrive\+\_\+t}} \texorpdfstring{$\ast$}{*}p, int motor\+\_\+number, float velocity)
\begin{DoxyCompactList}\small\item\em Sends ASCII command to send velocity setpoint to ODrive. \end{DoxyCompactList}\item 
void \mbox{\hyperlink{odrive__wrapper_8h_a6fff222e9c4e938392faacf4cccd1925}{ODRIVE\+\_\+\+Set\+Torque}} (\mbox{\hyperlink{structodrive__t}{odrive\+\_\+t}} \texorpdfstring{$\ast$}{*}p, int motor\+\_\+number, float torque)
\begin{DoxyCompactList}\small\item\em Sends ASCII command to send torque setpoint to ODrive. \end{DoxyCompactList}\item 
uint8\+\_\+t \texorpdfstring{$\ast$}{*} \mbox{\hyperlink{odrive__wrapper_8h_a42dae01f885677084b5223cb8a259b66}{ODRIVE\+\_\+\+Get\+Feedback}} (\mbox{\hyperlink{structodrive__t}{odrive\+\_\+t}} \texorpdfstring{$\ast$}{*}p, int motor\+\_\+number)
\begin{DoxyCompactList}\small\item\em Sends ASCII command to get current position and velocity from ODrive. \end{DoxyCompactList}\item 
uint8\+\_\+t \texorpdfstring{$\ast$}{*} \mbox{\hyperlink{odrive__wrapper_8h_a60cc06522e5b60f0383052c1f9cea4c5}{ODRIVE\+\_\+\+Get\+VBus}} (\mbox{\hyperlink{structodrive__t}{odrive\+\_\+t}} \texorpdfstring{$\ast$}{*}p)
\begin{DoxyCompactList}\small\item\em Sends ASCII command to get VBUS voltage from ODrive. \end{DoxyCompactList}\item 
uint8\+\_\+t \texorpdfstring{$\ast$}{*} \mbox{\hyperlink{odrive__wrapper_8h_aac7f31794321642f9aa5064b454f4799}{ODRIVE\+\_\+\+Is\+Calibrated}} (\mbox{\hyperlink{structodrive__t}{odrive\+\_\+t}} \texorpdfstring{$\ast$}{*}p)
\begin{DoxyCompactList}\small\item\em Sends ASCII command to check calibrated status ODrive. \end{DoxyCompactList}\item 
void \mbox{\hyperlink{odrive__wrapper_8h_a6ea52cd425986e041299100c9ce37564}{ODRIVE\+\_\+\+Write\+Param}} (\mbox{\hyperlink{structodrive__t}{odrive\+\_\+t}} \texorpdfstring{$\ast$}{*}p, char param\mbox{[}$\,$\mbox{]})
\begin{DoxyCompactList}\small\item\em Sends ASCII command to ODrive. \end{DoxyCompactList}\item 
uint8\+\_\+t \texorpdfstring{$\ast$}{*} \mbox{\hyperlink{odrive__wrapper_8h_ad14c9d5698a70cc0796f76190bdd1aa8}{ODRIVE\+\_\+\+Read\+Param}} (\mbox{\hyperlink{structodrive__t}{odrive\+\_\+t}} \texorpdfstring{$\ast$}{*}p, char param\mbox{[}$\,$\mbox{]})
\begin{DoxyCompactList}\small\item\em Receives ASCII command from ODrive. \end{DoxyCompactList}\item 
uint8\+\_\+t \texorpdfstring{$\ast$}{*} \mbox{\hyperlink{odrive__wrapper_8h_a15c8c6e4f8fd6ae104fff6063561fd57}{get\+Received\+String}} (\mbox{\hyperlink{structodrive__t}{odrive\+\_\+t}} \texorpdfstring{$\ast$}{*}P)
\begin{DoxyCompactList}\small\item\em Sends ASCII command to reboot ODrive. \end{DoxyCompactList}\item 
void \mbox{\hyperlink{odrive__wrapper_8h_ab6435b6238a1cb4ff3627f8736a86d72}{start\+\_\+receive\+\_\+string}} (\mbox{\hyperlink{structodrive__t}{odrive\+\_\+t}} \texorpdfstring{$\ast$}{*}p)
\begin{DoxyCompactList}\small\item\em Starts receiving a new string via UART. \end{DoxyCompactList}\item 
void \mbox{\hyperlink{odrive__wrapper_8h_a38cf8e45ebb6bf5c5afcfde2e0df6a89}{ODRIVE\+\_\+\+Receive\+\_\+\+Callback}} (UART\+\_\+\+Handle\+Type\+Def \texorpdfstring{$\ast$}{*}huart, \mbox{\hyperlink{structodrive__t}{odrive\+\_\+t}} \texorpdfstring{$\ast$}{*}p)
\begin{DoxyCompactList}\small\item\em Callback to properly receive strings via UART. \end{DoxyCompactList}\item 
void \mbox{\hyperlink{odrive__wrapper_8h_ac79567b84e267d7523601be2949e4d2c}{extract\+Floats}} (uint8\+\_\+t \texorpdfstring{$\ast$}{*}message, float \texorpdfstring{$\ast$}{*}pos, float \texorpdfstring{$\ast$}{*}vel)
\begin{DoxyCompactList}\small\item\em Extracts floats from a given string of two floats in ASCII protocol format. \end{DoxyCompactList}\end{DoxyCompactItemize}

\doxysubsection{Macro Definition Documentation}
\Hypertarget{odrive__wrapper_8h_a6b20d41d6252e9871430c242cb1a56e7}\index{odrive\_wrapper.h@{odrive\_wrapper.h}!BUFFER\_SIZE@{BUFFER\_SIZE}}
\index{BUFFER\_SIZE@{BUFFER\_SIZE}!odrive\_wrapper.h@{odrive\_wrapper.h}}
\doxysubsubsection{\texorpdfstring{BUFFER\_SIZE}{BUFFER\_SIZE}}
{\footnotesize\ttfamily \label{odrive__wrapper_8h_a6b20d41d6252e9871430c242cb1a56e7} 
\#define BUFFER\+\_\+\+SIZE~50}

\doxysubsection{Function Documentation}
\Hypertarget{odrive__wrapper_8h_ac79567b84e267d7523601be2949e4d2c}\index{odrive\_wrapper.h@{odrive\_wrapper.h}!extractFloats@{extractFloats}}
\index{extractFloats@{extractFloats}!odrive\_wrapper.h@{odrive\_wrapper.h}}
\doxysubsubsection{\texorpdfstring{extractFloats()}{extractFloats()}}
{\footnotesize\ttfamily \label{odrive__wrapper_8h_ac79567b84e267d7523601be2949e4d2c} 
void extract\+Floats (\begin{DoxyParamCaption}\item[{uint8\+\_\+t \texorpdfstring{$\ast$}{*}}]{message}{, }\item[{float \texorpdfstring{$\ast$}{*}}]{x}{, }\item[{float \texorpdfstring{$\ast$}{*}}]{y}{}\end{DoxyParamCaption})}

Extracts floats from a given string of two floats in ASCII protocol format. 

For use in converting feedback message. 
\begin{DoxyParams}{Parameters}
{\em message} & Pointer to the received message. \\
\hline
{\em x} & Pointer to a first float. \\
\hline
{\em y} & Pointer to a second float. \\
\hline
\end{DoxyParams}
\Hypertarget{odrive__wrapper_8h_a15c8c6e4f8fd6ae104fff6063561fd57}\index{odrive\_wrapper.h@{odrive\_wrapper.h}!getReceivedString@{getReceivedString}}
\index{getReceivedString@{getReceivedString}!odrive\_wrapper.h@{odrive\_wrapper.h}}
\doxysubsubsection{\texorpdfstring{getReceivedString()}{getReceivedString()}}
{\footnotesize\ttfamily \label{odrive__wrapper_8h_a15c8c6e4f8fd6ae104fff6063561fd57} 
uint8\+\_\+t \texorpdfstring{$\ast$}{*} get\+Received\+String (\begin{DoxyParamCaption}\item[{\mbox{\hyperlink{structodrive__t}{odrive\+\_\+t}} \texorpdfstring{$\ast$}{*}}]{p}{}\end{DoxyParamCaption})}

Sends ASCII command to reboot ODrive. 

\begin{DoxyParams}{Parameters}
{\em p} & Pointer to an ODrive object. \\
\hline
\end{DoxyParams}
\Hypertarget{odrive__wrapper_8h_ab13b958603fb943556b9a7c32fc95bac}\index{odrive\_wrapper.h@{odrive\_wrapper.h}!ODRIVE\_ClearErrors@{ODRIVE\_ClearErrors}}
\index{ODRIVE\_ClearErrors@{ODRIVE\_ClearErrors}!odrive\_wrapper.h@{odrive\_wrapper.h}}
\doxysubsubsection{\texorpdfstring{ODRIVE\_ClearErrors()}{ODRIVE\_ClearErrors()}}
{\footnotesize\ttfamily \label{odrive__wrapper_8h_ab13b958603fb943556b9a7c32fc95bac} 
void ODRIVE\+\_\+\+Clear\+Errors (\begin{DoxyParamCaption}\item[{\mbox{\hyperlink{structodrive__t}{odrive\+\_\+t}} \texorpdfstring{$\ast$}{*}}]{p}{}\end{DoxyParamCaption})}

Sends ASCII command to clear errors on ODrive. 

\begin{DoxyParams}{Parameters}
{\em p} & Pointer to an ODrive object. \\
\hline
\end{DoxyParams}
\Hypertarget{odrive__wrapper_8h_a42dae01f885677084b5223cb8a259b66}\index{odrive\_wrapper.h@{odrive\_wrapper.h}!ODRIVE\_GetFeedback@{ODRIVE\_GetFeedback}}
\index{ODRIVE\_GetFeedback@{ODRIVE\_GetFeedback}!odrive\_wrapper.h@{odrive\_wrapper.h}}
\doxysubsubsection{\texorpdfstring{ODRIVE\_GetFeedback()}{ODRIVE\_GetFeedback()}}
{\footnotesize\ttfamily \label{odrive__wrapper_8h_a42dae01f885677084b5223cb8a259b66} 
uint8\+\_\+t \texorpdfstring{$\ast$}{*} ODRIVE\+\_\+\+Get\+Feedback (\begin{DoxyParamCaption}\item[{\mbox{\hyperlink{structodrive__t}{odrive\+\_\+t}} \texorpdfstring{$\ast$}{*}}]{p}{, }\item[{int}]{motor\+\_\+number}{}\end{DoxyParamCaption})}

Sends ASCII command to get current position and velocity from ODrive. 

\begin{DoxyParams}{Parameters}
{\em p} & Pointer to an ODrive object. \\
\hline
{\em motor\+\_\+number} & Motor number on ODrive. Typically 0. \\
\hline
\end{DoxyParams}
\Hypertarget{odrive__wrapper_8h_a60cc06522e5b60f0383052c1f9cea4c5}\index{odrive\_wrapper.h@{odrive\_wrapper.h}!ODRIVE\_GetVBus@{ODRIVE\_GetVBus}}
\index{ODRIVE\_GetVBus@{ODRIVE\_GetVBus}!odrive\_wrapper.h@{odrive\_wrapper.h}}
\doxysubsubsection{\texorpdfstring{ODRIVE\_GetVBus()}{ODRIVE\_GetVBus()}}
{\footnotesize\ttfamily \label{odrive__wrapper_8h_a60cc06522e5b60f0383052c1f9cea4c5} 
uint8\+\_\+t \texorpdfstring{$\ast$}{*} ODRIVE\+\_\+\+Get\+VBus (\begin{DoxyParamCaption}\item[{\mbox{\hyperlink{structodrive__t}{odrive\+\_\+t}} \texorpdfstring{$\ast$}{*}}]{p}{}\end{DoxyParamCaption})}

Sends ASCII command to get VBUS voltage from ODrive. 

Used mainly as a test to see if we can send and receive UART commands. 
\begin{DoxyParams}{Parameters}
{\em p} & Pointer to an ODrive object. \\
\hline
\end{DoxyParams}
\Hypertarget{odrive__wrapper_8h_aac7f31794321642f9aa5064b454f4799}\index{odrive\_wrapper.h@{odrive\_wrapper.h}!ODRIVE\_IsCalibrated@{ODRIVE\_IsCalibrated}}
\index{ODRIVE\_IsCalibrated@{ODRIVE\_IsCalibrated}!odrive\_wrapper.h@{odrive\_wrapper.h}}
\doxysubsubsection{\texorpdfstring{ODRIVE\_IsCalibrated()}{ODRIVE\_IsCalibrated()}}
{\footnotesize\ttfamily \label{odrive__wrapper_8h_aac7f31794321642f9aa5064b454f4799} 
uint8\+\_\+t \texorpdfstring{$\ast$}{*} ODRIVE\+\_\+\+Is\+Calibrated (\begin{DoxyParamCaption}\item[{\mbox{\hyperlink{structodrive__t}{odrive\+\_\+t}} \texorpdfstring{$\ast$}{*}}]{p}{}\end{DoxyParamCaption})}

Sends ASCII command to check calibrated status ODrive. 

I think this one is broken. 
\begin{DoxyParams}{Parameters}
{\em p} & Pointer to an ODrive object. \\
\hline
\end{DoxyParams}
\Hypertarget{odrive__wrapper_8h_ad14c9d5698a70cc0796f76190bdd1aa8}\index{odrive\_wrapper.h@{odrive\_wrapper.h}!ODRIVE\_ReadParam@{ODRIVE\_ReadParam}}
\index{ODRIVE\_ReadParam@{ODRIVE\_ReadParam}!odrive\_wrapper.h@{odrive\_wrapper.h}}
\doxysubsubsection{\texorpdfstring{ODRIVE\_ReadParam()}{ODRIVE\_ReadParam()}}
{\footnotesize\ttfamily \label{odrive__wrapper_8h_ad14c9d5698a70cc0796f76190bdd1aa8} 
uint8\+\_\+t \texorpdfstring{$\ast$}{*} ODRIVE\+\_\+\+Read\+Param (\begin{DoxyParamCaption}\item[{\mbox{\hyperlink{structodrive__t}{odrive\+\_\+t}} \texorpdfstring{$\ast$}{*}}]{p}{, }\item[{char}]{param}{\mbox{[}$\,$\mbox{]}}\end{DoxyParamCaption})}

Receives ASCII command from ODrive. 

\begin{DoxyParams}{Parameters}
{\em p} & Pointer to an ODrive object. \\
\hline
{\em param\mbox{[}$\,$\mbox{]}} & Parameter to read from, in string format. \\
\hline
\end{DoxyParams}
\Hypertarget{odrive__wrapper_8h_a25d657b24b80292f58a570b02e7aa428}\index{odrive\_wrapper.h@{odrive\_wrapper.h}!ODRIVE\_Reboot@{ODRIVE\_Reboot}}
\index{ODRIVE\_Reboot@{ODRIVE\_Reboot}!odrive\_wrapper.h@{odrive\_wrapper.h}}
\doxysubsubsection{\texorpdfstring{ODRIVE\_Reboot()}{ODRIVE\_Reboot()}}
{\footnotesize\ttfamily \label{odrive__wrapper_8h_a25d657b24b80292f58a570b02e7aa428} 
void ODRIVE\+\_\+\+Reboot (\begin{DoxyParamCaption}\item[{\mbox{\hyperlink{structodrive__t}{odrive\+\_\+t}} \texorpdfstring{$\ast$}{*}}]{p}{}\end{DoxyParamCaption})}

Sends ASCII command to reboot ODrive. 

\begin{DoxyParams}{Parameters}
{\em p} & Pointer to an ODrive object. \\
\hline
\end{DoxyParams}
\Hypertarget{odrive__wrapper_8h_a38cf8e45ebb6bf5c5afcfde2e0df6a89}\index{odrive\_wrapper.h@{odrive\_wrapper.h}!ODRIVE\_Receive\_Callback@{ODRIVE\_Receive\_Callback}}
\index{ODRIVE\_Receive\_Callback@{ODRIVE\_Receive\_Callback}!odrive\_wrapper.h@{odrive\_wrapper.h}}
\doxysubsubsection{\texorpdfstring{ODRIVE\_Receive\_Callback()}{ODRIVE\_Receive\_Callback()}}
{\footnotesize\ttfamily \label{odrive__wrapper_8h_a38cf8e45ebb6bf5c5afcfde2e0df6a89} 
void ODRIVE\+\_\+\+Receive\+\_\+\+Callback (\begin{DoxyParamCaption}\item[{UART\+\_\+\+Handle\+Type\+Def \texorpdfstring{$\ast$}{*}}]{huart}{, }\item[{\mbox{\hyperlink{structodrive__t}{odrive\+\_\+t}} \texorpdfstring{$\ast$}{*}}]{p}{}\end{DoxyParamCaption})}

Callback to properly receive strings via UART. 

\begin{DoxyParams}{Parameters}
{\em p} & Pointer to an ODrive object. \\
\hline
{\em huart} & UART object that is compared to ODrive object to confirm they are the same. \\
\hline
\end{DoxyParams}
\Hypertarget{odrive__wrapper_8h_a7b3454ebe0e4fdd3a2a0dc64f72719c9}\index{odrive\_wrapper.h@{odrive\_wrapper.h}!ODRIVE\_SetPosition@{ODRIVE\_SetPosition}}
\index{ODRIVE\_SetPosition@{ODRIVE\_SetPosition}!odrive\_wrapper.h@{odrive\_wrapper.h}}
\doxysubsubsection{\texorpdfstring{ODRIVE\_SetPosition()}{ODRIVE\_SetPosition()}}
{\footnotesize\ttfamily \label{odrive__wrapper_8h_a7b3454ebe0e4fdd3a2a0dc64f72719c9} 
void ODRIVE\+\_\+\+Set\+Position (\begin{DoxyParamCaption}\item[{\mbox{\hyperlink{structodrive__t}{odrive\+\_\+t}} \texorpdfstring{$\ast$}{*}}]{p}{, }\item[{int}]{motor\+\_\+number}{, }\item[{float}]{position}{, }\item[{float}]{velocity\+\_\+lim}{, }\item[{float}]{torque\+\_\+lim}{}\end{DoxyParamCaption})}

Sends ASCII command to send position setpoint to ODrive. 

\begin{DoxyParams}{Parameters}
{\em p} & Pointer to an ODrive object. \\
\hline
{\em motor\+\_\+number} & Motor number on ODrive. Typically 0. \\
\hline
{\em position} & Position setpoint \\
\hline
{\em velocity\+\_\+lim} & Velocity limit \\
\hline
{\em torque\+\_\+lim} & Torque limit \\
\hline
\end{DoxyParams}
\Hypertarget{odrive__wrapper_8h_a18367d959b193c49f6c7534cc7ab857f}\index{odrive\_wrapper.h@{odrive\_wrapper.h}!ODRIVE\_SetPositionFF@{ODRIVE\_SetPositionFF}}
\index{ODRIVE\_SetPositionFF@{ODRIVE\_SetPositionFF}!odrive\_wrapper.h@{odrive\_wrapper.h}}
\doxysubsubsection{\texorpdfstring{ODRIVE\_SetPositionFF()}{ODRIVE\_SetPositionFF()}}
{\footnotesize\ttfamily \label{odrive__wrapper_8h_a18367d959b193c49f6c7534cc7ab857f} 
void ODRIVE\+\_\+\+Set\+Position\+FF (\begin{DoxyParamCaption}\item[{\mbox{\hyperlink{structodrive__t}{odrive\+\_\+t}} \texorpdfstring{$\ast$}{*}}]{p}{, }\item[{int}]{motor\+\_\+number}{, }\item[{float}]{position}{, }\item[{float}]{velocity\+\_\+feedforward}{, }\item[{float}]{current\+\_\+feedforward}{}\end{DoxyParamCaption})}

Sends ASCII command to send position setpoint with feedforward ODrive. 

\begin{DoxyParams}{Parameters}
{\em p} & Pointer to an ODrive object. \\
\hline
{\em motor\+\_\+number} & Motor number on ODrive. Typically 0. \\
\hline
{\em position} & Position setpoint \\
\hline
{\em velocity\+\_\+feedforward} & Velocity feedforward value. \\
\hline
{\em current\+\_\+feedforward} & Current feedforward value. \\
\hline
\end{DoxyParams}
\Hypertarget{odrive__wrapper_8h_a6fff222e9c4e938392faacf4cccd1925}\index{odrive\_wrapper.h@{odrive\_wrapper.h}!ODRIVE\_SetTorque@{ODRIVE\_SetTorque}}
\index{ODRIVE\_SetTorque@{ODRIVE\_SetTorque}!odrive\_wrapper.h@{odrive\_wrapper.h}}
\doxysubsubsection{\texorpdfstring{ODRIVE\_SetTorque()}{ODRIVE\_SetTorque()}}
{\footnotesize\ttfamily \label{odrive__wrapper_8h_a6fff222e9c4e938392faacf4cccd1925} 
void ODRIVE\+\_\+\+Set\+Torque (\begin{DoxyParamCaption}\item[{\mbox{\hyperlink{structodrive__t}{odrive\+\_\+t}} \texorpdfstring{$\ast$}{*}}]{p}{, }\item[{int}]{motor\+\_\+number}{, }\item[{float}]{torque}{}\end{DoxyParamCaption})}

Sends ASCII command to send torque setpoint to ODrive. 

\begin{DoxyParams}{Parameters}
{\em p} & Pointer to an ODrive object. \\
\hline
{\em motor\+\_\+number} & Motor number on ODrive. Typically 0. \\
\hline
{\em torque} & Torque setpoint. \\
\hline
\end{DoxyParams}
\Hypertarget{odrive__wrapper_8h_a896ffd1031a488a9f22fd92ff20bd384}\index{odrive\_wrapper.h@{odrive\_wrapper.h}!ODRIVE\_SetVelocity@{ODRIVE\_SetVelocity}}
\index{ODRIVE\_SetVelocity@{ODRIVE\_SetVelocity}!odrive\_wrapper.h@{odrive\_wrapper.h}}
\doxysubsubsection{\texorpdfstring{ODRIVE\_SetVelocity()}{ODRIVE\_SetVelocity()}}
{\footnotesize\ttfamily \label{odrive__wrapper_8h_a896ffd1031a488a9f22fd92ff20bd384} 
void ODRIVE\+\_\+\+Set\+Velocity (\begin{DoxyParamCaption}\item[{\mbox{\hyperlink{structodrive__t}{odrive\+\_\+t}} \texorpdfstring{$\ast$}{*}}]{p}{, }\item[{int}]{motor\+\_\+number}{, }\item[{float}]{velocity}{}\end{DoxyParamCaption})}

Sends ASCII command to send velocity setpoint to ODrive. 

\begin{DoxyParams}{Parameters}
{\em p} & Pointer to an ODrive object. \\
\hline
{\em motor\+\_\+number} & Motor number on ODrive. Typically 0. \\
\hline
{\em velocity} & Velocity setpoint. \\
\hline
\end{DoxyParams}
\Hypertarget{odrive__wrapper_8h_a6ea52cd425986e041299100c9ce37564}\index{odrive\_wrapper.h@{odrive\_wrapper.h}!ODRIVE\_WriteParam@{ODRIVE\_WriteParam}}
\index{ODRIVE\_WriteParam@{ODRIVE\_WriteParam}!odrive\_wrapper.h@{odrive\_wrapper.h}}
\doxysubsubsection{\texorpdfstring{ODRIVE\_WriteParam()}{ODRIVE\_WriteParam()}}
{\footnotesize\ttfamily \label{odrive__wrapper_8h_a6ea52cd425986e041299100c9ce37564} 
void ODRIVE\+\_\+\+Write\+Param (\begin{DoxyParamCaption}\item[{\mbox{\hyperlink{structodrive__t}{odrive\+\_\+t}} \texorpdfstring{$\ast$}{*}}]{p}{, }\item[{char}]{param}{\mbox{[}$\,$\mbox{]}}\end{DoxyParamCaption})}

Sends ASCII command to ODrive. 

\begin{DoxyParams}{Parameters}
{\em p} & Pointer to an ODrive object. \\
\hline
{\em param\mbox{[}$\,$\mbox{]}} & Parameter to write to, in string format. \\
\hline
\end{DoxyParams}
\Hypertarget{odrive__wrapper_8h_ab6435b6238a1cb4ff3627f8736a86d72}\index{odrive\_wrapper.h@{odrive\_wrapper.h}!start\_receive\_string@{start\_receive\_string}}
\index{start\_receive\_string@{start\_receive\_string}!odrive\_wrapper.h@{odrive\_wrapper.h}}
\doxysubsubsection{\texorpdfstring{start\_receive\_string()}{start\_receive\_string()}}
{\footnotesize\ttfamily \label{odrive__wrapper_8h_ab6435b6238a1cb4ff3627f8736a86d72} 
void start\+\_\+receive\+\_\+string (\begin{DoxyParamCaption}\item[{\mbox{\hyperlink{structodrive__t}{odrive\+\_\+t}} \texorpdfstring{$\ast$}{*}}]{p}{}\end{DoxyParamCaption})}

Starts receiving a new string via UART. 

Sets the buffer index to zero and sets up HAL\+\_\+\+UART\+\_\+\+Receive correctly for the ODrive object. 
\begin{DoxyParams}{Parameters}
{\em p} & Pointer to an ODrive object. \\
\hline
\end{DoxyParams}

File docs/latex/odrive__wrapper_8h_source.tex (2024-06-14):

\doxysection{odrive\+\_\+wrapper.\+h}
\hypertarget{odrive__wrapper_8h_source}{}\label{odrive__wrapper_8h_source}\index{odrive\_wrapper.h@{odrive\_wrapper.h}}
\mbox{\hyperlink{odrive__wrapper_8h}{Go to the documentation of this file.}}
\begin{DoxyCode}{0}
\DoxyCodeLine{00001\ \textcolor{comment}{/*}}
\DoxyCodeLine{00002\ \textcolor{comment}{\ *\ odrive\_wrapper.h}}
\DoxyCodeLine{00003\ \textcolor{comment}{\ *}}
\DoxyCodeLine{00004\ \textcolor{comment}{\ *\ \ Created\ on:\ May\ 20,\ 2024}}
\DoxyCodeLine{00005\ \textcolor{comment}{\ *\ \ \ \ \ \ Author:\ Aidan}}
\DoxyCodeLine{00006\ \textcolor{comment}{\ */}}
\DoxyCodeLine{00007\ }
\DoxyCodeLine{00008\ \textcolor{preprocessor}{\#ifndef\ INC\_ODRIVE\_WRAPPER\_H\_}}
\DoxyCodeLine{00009\ \textcolor{preprocessor}{\#define\ INC\_ODRIVE\_WRAPPER\_H\_}}
\DoxyCodeLine{00010\ }
\DoxyCodeLine{00011\ \textcolor{preprocessor}{\#include\ "{}\mbox{\hyperlink{main_8h}{main.h}}"{}}}
\DoxyCodeLine{00012\ }
\DoxyCodeLine{00013\ \textcolor{preprocessor}{\#define\ BUFFER\_SIZE\ 50}}
\DoxyCodeLine{00014\ }
\DoxyCodeLine{00015\ \textcolor{keyword}{struct\ }odrive\_struct\ \{}
\DoxyCodeLine{00016\ }
\DoxyCodeLine{00017\ \ \ \ \ UART\_HandleTypeDef*\ \mbox{\hyperlink{structodrive__t_a1ed7dab212fde0a3a4600d33399c67b6}{huart}};}
\DoxyCodeLine{00018\ }
\DoxyCodeLine{00019\ \}\ \textcolor{keyword}{typedef}\ \mbox{\hyperlink{structodrive__t}{odrive\_t}};}
\DoxyCodeLine{00020\ }
\DoxyCodeLine{00021\ }
\DoxyCodeLine{00022\ \textcolor{comment}{//\ following\ is\ an\ implementation\ of\ the\ useful\ commands\ from\ here:}}
\DoxyCodeLine{00023\ \textcolor{comment}{//\ https://docs.odriverobotics.com/v/latest/manual/ascii-\/protocol.html}}
\DoxyCodeLine{00024\ \textcolor{comment}{//\ all\ commands\ follow\ as\ ASCII\ protocol,\ formatted\ as\ so:}}
\DoxyCodeLine{00025\ \textcolor{comment}{//\ command\ *42\ ;\ comment\ [new\ line\ character],\ where\ *42\ is\ a\ non-\/required\ checksum}}
\DoxyCodeLine{00026\ }
\DoxyCodeLine{00027\ \textcolor{comment}{//\ prototype\ functions}}
\DoxyCodeLine{00028\ \textcolor{comment}{//\ commands\ to\ odrive\ controller}}
\DoxyCodeLine{00029\ \textcolor{keywordtype}{void}\ \mbox{\hyperlink{odrive__wrapper_8h_a25d657b24b80292f58a570b02e7aa428}{ODRIVE\_Reboot}}(\mbox{\hyperlink{structodrive__t}{odrive\_t}}\ *p);}
\DoxyCodeLine{00030\ \textcolor{keywordtype}{void}\ \mbox{\hyperlink{odrive__wrapper_8h_ab13b958603fb943556b9a7c32fc95bac}{ODRIVE\_ClearErrors}}(\mbox{\hyperlink{structodrive__t}{odrive\_t}}\ *p);}
\DoxyCodeLine{00031\ }
\DoxyCodeLine{00032\ \textcolor{comment}{//\ functions\ for\ motor\ control}}
\DoxyCodeLine{00033\ \textcolor{keywordtype}{void}\ \mbox{\hyperlink{odrive__wrapper_8h_a7b3454ebe0e4fdd3a2a0dc64f72719c9}{ODRIVE\_SetPosition}}(\mbox{\hyperlink{structodrive__t}{odrive\_t}}\ *p,\ \textcolor{keywordtype}{int}\ motor\_number,\ \textcolor{keywordtype}{float}\ position,\ \textcolor{keywordtype}{float}\ velocity\_lim,\ \textcolor{keywordtype}{float}\ torque\_lim);}
\DoxyCodeLine{00034\ \textcolor{keywordtype}{void}\ \mbox{\hyperlink{odrive__wrapper_8h_a18367d959b193c49f6c7534cc7ab857f}{ODRIVE\_SetPositionFF}}(\mbox{\hyperlink{structodrive__t}{odrive\_t}}\ *p,\ \textcolor{keywordtype}{int}\ motor\_number,\ \textcolor{keywordtype}{float}\ position,\ \textcolor{keywordtype}{float}\ velocity\_feedforward,\ \textcolor{keywordtype}{float}\ current\_feedforward);}
\DoxyCodeLine{00035\ \textcolor{keywordtype}{void}\ \mbox{\hyperlink{odrive__wrapper_8h_a896ffd1031a488a9f22fd92ff20bd384}{ODRIVE\_SetVelocity}}(\mbox{\hyperlink{structodrive__t}{odrive\_t}}\ *p,\ \textcolor{keywordtype}{int}\ motor\_number,\ \textcolor{keywordtype}{float}\ velocity);}
\DoxyCodeLine{00036\ \textcolor{keywordtype}{void}\ \mbox{\hyperlink{odrive__wrapper_8h_a6fff222e9c4e938392faacf4cccd1925}{ODRIVE\_SetTorque}}(\mbox{\hyperlink{structodrive__t}{odrive\_t}}\ *p,\ \textcolor{keywordtype}{int}\ motor\_number,\ \textcolor{keywordtype}{float}\ torque);}
\DoxyCodeLine{00037\ uint8\_t*\ \mbox{\hyperlink{odrive__wrapper_8h_a42dae01f885677084b5223cb8a259b66}{ODRIVE\_GetFeedback}}(\mbox{\hyperlink{structodrive__t}{odrive\_t}}\ *p,\ \textcolor{keywordtype}{int}\ motor\_number);\ \textcolor{comment}{//\ returns\ "{}pos\ vel"{}}}
\DoxyCodeLine{00038\ }
\DoxyCodeLine{00039\ \textcolor{comment}{//\ paramater\ reading\ and\ writing}}
\DoxyCodeLine{00040\ uint8\_t*\ \mbox{\hyperlink{odrive__wrapper_8h_a60cc06522e5b60f0383052c1f9cea4c5}{ODRIVE\_GetVBus}}(\mbox{\hyperlink{structodrive__t}{odrive\_t}}\ *p);\ \textcolor{comment}{//\ functionally\ equivalent\ to\ the\ read\ param\ but\ used\ enough\ that\ it\ is\ its\ own\ function}}
\DoxyCodeLine{00041\ uint8\_t*\ \mbox{\hyperlink{odrive__wrapper_8h_aac7f31794321642f9aa5064b454f4799}{ODRIVE\_IsCalibrated}}(\mbox{\hyperlink{structodrive__t}{odrive\_t}}\ *p);}
\DoxyCodeLine{00042\ \textcolor{keywordtype}{void}\ \mbox{\hyperlink{odrive__wrapper_8h_a6ea52cd425986e041299100c9ce37564}{ODRIVE\_WriteParam}}(\mbox{\hyperlink{structodrive__t}{odrive\_t}}\ *p,\ \textcolor{keywordtype}{char}\ param[]);}
\DoxyCodeLine{00043\ uint8\_t*\ \mbox{\hyperlink{odrive__wrapper_8h_ad14c9d5698a70cc0796f76190bdd1aa8}{ODRIVE\_ReadParam}}(\mbox{\hyperlink{structodrive__t}{odrive\_t}}\ *p,\ \textcolor{keywordtype}{char}\ param[]);}
\DoxyCodeLine{00044\ }
\DoxyCodeLine{00045\ \textcolor{comment}{//\ generic\ send\ /\ receive\ functions}}
\DoxyCodeLine{00046\ uint8\_t*\ \mbox{\hyperlink{odrive__wrapper_8h_a15c8c6e4f8fd6ae104fff6063561fd57}{getReceivedString}}(\mbox{\hyperlink{structodrive__t}{odrive\_t}}\ *P);}
\DoxyCodeLine{00047\ \textcolor{keywordtype}{void}\ \mbox{\hyperlink{odrive__wrapper_8h_ab6435b6238a1cb4ff3627f8736a86d72}{start\_receive\_string}}(\mbox{\hyperlink{structodrive__t}{odrive\_t}}\ *p);}
\DoxyCodeLine{00048\ \textcolor{keywordtype}{void}\ \mbox{\hyperlink{odrive__wrapper_8h_a38cf8e45ebb6bf5c5afcfde2e0df6a89}{ODRIVE\_Receive\_Callback}}\ (UART\_HandleTypeDef\ *huart,\ \mbox{\hyperlink{structodrive__t}{odrive\_t}}\ *p);}
\DoxyCodeLine{00049\ \textcolor{keywordtype}{void}\ \mbox{\hyperlink{odrive__wrapper_8h_ac79567b84e267d7523601be2949e4d2c}{extractFloats}}(uint8\_t*\ message,\ \textcolor{keywordtype}{float}*\ pos,\ \textcolor{keywordtype}{float}*\ vel);}
\DoxyCodeLine{00050\ }
\DoxyCodeLine{00051\ \textcolor{preprocessor}{\#endif\ }\textcolor{comment}{/*\ INC\_ODRIVE\_WRAPPER\_H\_\ */}\textcolor{preprocessor}{}}

\end{DoxyCode}

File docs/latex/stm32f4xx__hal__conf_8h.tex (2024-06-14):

\doxysection{stm32f4xx\+\_\+hal\+\_\+conf.\+h File Reference}
\hypertarget{stm32f4xx__hal__conf_8h}{}\label{stm32f4xx__hal__conf_8h}\index{stm32f4xx\_hal\_conf.h@{stm32f4xx\_hal\_conf.h}}
{\ttfamily \#include "{}stm32f4xx\+\_\+hal\+\_\+rcc.\+h"{}}\newline
{\ttfamily \#include "{}stm32f4xx\+\_\+hal\+\_\+gpio.\+h"{}}\newline
{\ttfamily \#include "{}stm32f4xx\+\_\+hal\+\_\+exti.\+h"{}}\newline
{\ttfamily \#include "{}stm32f4xx\+\_\+hal\+\_\+dma.\+h"{}}\newline
{\ttfamily \#include "{}stm32f4xx\+\_\+hal\+\_\+cortex.\+h"{}}\newline
{\ttfamily \#include "{}stm32f4xx\+\_\+hal\+\_\+flash.\+h"{}}\newline
{\ttfamily \#include "{}stm32f4xx\+\_\+hal\+\_\+i2c.\+h"{}}\newline
{\ttfamily \#include "{}stm32f4xx\+\_\+hal\+\_\+pwr.\+h"{}}\newline
{\ttfamily \#include "{}stm32f4xx\+\_\+hal\+\_\+tim.\+h"{}}\newline
{\ttfamily \#include "{}stm32f4xx\+\_\+hal\+\_\+uart.\+h"{}}\newline
Include dependency graph for stm32f4xx\+\_\+hal\+\_\+conf.\+h\+:\nopagebreak
\begin{figure}[H]
\begin{center}
\leavevmode

\end{center}
\end{figure}
\doxysubsubsection*{Macros}
\begin{DoxyCompactItemize}
\item 
\#define \mbox{\hyperlink{stm32f4xx__hal__conf_8h_a877ae99e8c47a609ea97c888912bf75f}{HAL\+\_\+\+MODULE\+\_\+\+ENABLED}}
\begin{DoxyCompactList}\small\item\em This is the list of modules to be used in the HAL driver. \end{DoxyCompactList}\item 
\#define \mbox{\hyperlink{stm32f4xx__hal__conf_8h_a19999766418b0224871f732d800841c6}{HAL\+\_\+\+I2\+C\+\_\+\+MODULE\+\_\+\+ENABLED}}
\item 
\#define \mbox{\hyperlink{stm32f4xx__hal__conf_8h_a23382b8f04b3e6db2c59dfa1ef5ea4a2}{HAL\+\_\+\+TIM\+\_\+\+MODULE\+\_\+\+ENABLED}}
\item 
\#define \mbox{\hyperlink{stm32f4xx__hal__conf_8h_a167269406e73327b95c3bb7b9cfe6d89}{HAL\+\_\+\+UART\+\_\+\+MODULE\+\_\+\+ENABLED}}
\item 
\#define \mbox{\hyperlink{stm32f4xx__hal__conf_8h_a86165f80d6078719ee0715afe13febf5}{HAL\+\_\+\+GPIO\+\_\+\+MODULE\+\_\+\+ENABLED}}
\item 
\#define \mbox{\hyperlink{stm32f4xx__hal__conf_8h_aeb359e861d8a92c233c3229657dbcd74}{HAL\+\_\+\+EXTI\+\_\+\+MODULE\+\_\+\+ENABLED}}
\item 
\#define \mbox{\hyperlink{stm32f4xx__hal__conf_8h_a6552186102a1131b2849ac55a582945d}{HAL\+\_\+\+DMA\+\_\+\+MODULE\+\_\+\+ENABLED}}
\item 
\#define \mbox{\hyperlink{stm32f4xx__hal__conf_8h_ac3dd74314ed62ac8575e2f9f48b3ac48}{HAL\+\_\+\+RCC\+\_\+\+MODULE\+\_\+\+ENABLED}}
\item 
\#define \mbox{\hyperlink{stm32f4xx__hal__conf_8h_a7112575efe3740911f19a13e6b170fee}{HAL\+\_\+\+FLASH\+\_\+\+MODULE\+\_\+\+ENABLED}}
\item 
\#define \mbox{\hyperlink{stm32f4xx__hal__conf_8h_ab51923c3716977d7923f49cc9d081aa8}{HAL\+\_\+\+PWR\+\_\+\+MODULE\+\_\+\+ENABLED}}
\item 
\#define \mbox{\hyperlink{stm32f4xx__hal__conf_8h_aa9b5a3a425901e097de70092dbe31e0f}{HAL\+\_\+\+CORTEX\+\_\+\+MODULE\+\_\+\+ENABLED}}
\item 
\#define \mbox{\hyperlink{stm32f4xx__hal__conf_8h_aeafcff4f57440c60e64812dddd13e7cb}{HSE\+\_\+\+VALUE}}~8000000U
\begin{DoxyCompactList}\small\item\em Adjust the value of External High Speed oscillator (HSE) used in your application. \end{DoxyCompactList}\item 
\#define \mbox{\hyperlink{stm32f4xx__hal__conf_8h_a68ecbc9b0a1a40a1ec9d18d5e9747c4f}{HSE\+\_\+\+STARTUP\+\_\+\+TIMEOUT}}~100U
\item 
\#define \mbox{\hyperlink{stm32f4xx__hal__conf_8h_aaa8c76e274d0f6dd2cefb5d0b17fbc37}{HSI\+\_\+\+VALUE}}~((uint32\+\_\+t)16000000U)
\begin{DoxyCompactList}\small\item\em Internal High Speed oscillator (HSI) value. \end{DoxyCompactList}\item 
\#define \mbox{\hyperlink{stm32f4xx__hal__conf_8h_a4872023e65449c0506aac3ea6bec99e9}{LSI\+\_\+\+VALUE}}~32000U
\begin{DoxyCompactList}\small\item\em Internal Low Speed oscillator (LSI) value. \end{DoxyCompactList}\item 
\#define \mbox{\hyperlink{stm32f4xx__hal__conf_8h_a7bbb9d19e5189a6ccd0fb6fa6177d20d}{LSE\+\_\+\+VALUE}}~32768U
\begin{DoxyCompactList}\small\item\em External Low Speed oscillator (LSE) value. \end{DoxyCompactList}\item 
\#define \mbox{\hyperlink{stm32f4xx__hal__conf_8h_a85e6fc812dc26f7161a04be2568a5462}{LSE\+\_\+\+STARTUP\+\_\+\+TIMEOUT}}~5000U
\item 
\#define \mbox{\hyperlink{stm32f4xx__hal__conf_8h_a8c47c935e91e70569098b41718558648}{EXTERNAL\+\_\+\+CLOCK\+\_\+\+VALUE}}~12288000U
\begin{DoxyCompactList}\small\item\em External clock source for I2S peripheral This value is used by the I2S HAL module to compute the I2S clock source frequency, this source is inserted directly through I2\+S\+\_\+\+CKIN pad. \end{DoxyCompactList}\item 
\#define \mbox{\hyperlink{stm32f4xx__hal__conf_8h_aae550dad9f96d52cfce5e539adadbbb4}{VDD\+\_\+\+VALUE}}~3300U
\begin{DoxyCompactList}\small\item\em This is the HAL system configuration section. \end{DoxyCompactList}\item 
\#define \mbox{\hyperlink{stm32f4xx__hal__conf_8h_ae27809d4959b9fd5b5d974e3e1c77d2e}{TICK\+\_\+\+INT\+\_\+\+PRIORITY}}~15U
\item 
\#define \mbox{\hyperlink{stm32f4xx__hal__conf_8h_ad048ac737242c2c2cb9f4a72953d10ce}{USE\+\_\+\+RTOS}}~0U
\item 
\#define \mbox{\hyperlink{stm32f4xx__hal__conf_8h_a13fc0d5e7bb925385c0cc0772ba6a391}{PREFETCH\+\_\+\+ENABLE}}~1U
\item 
\#define \mbox{\hyperlink{stm32f4xx__hal__conf_8h_a3379989d46599c7e19a43f42e9145a4a}{INSTRUCTION\+\_\+\+CACHE\+\_\+\+ENABLE}}~1U
\item 
\#define \mbox{\hyperlink{stm32f4xx__hal__conf_8h_a5b4c32a40cf49b06c0d761e385949a6b}{DATA\+\_\+\+CACHE\+\_\+\+ENABLE}}~1U
\item 
\#define \mbox{\hyperlink{stm32f4xx__hal__conf_8h_acc33abd5393affd16cc4a1397839dfe4}{USE\+\_\+\+HAL\+\_\+\+ADC\+\_\+\+REGISTER\+\_\+\+CALLBACKS}}~0U /\texorpdfstring{$\ast$}{*} ADC register callback disabled       \texorpdfstring{$\ast$}{*}/
\item 
\#define \mbox{\hyperlink{stm32f4xx__hal__conf_8h_a7f6bf06dfbf91fd866a9d62ab54d0e81}{USE\+\_\+\+HAL\+\_\+\+CAN\+\_\+\+REGISTER\+\_\+\+CALLBACKS}}~0U /\texorpdfstring{$\ast$}{*} CAN register callback disabled       \texorpdfstring{$\ast$}{*}/
\item 
\#define \mbox{\hyperlink{stm32f4xx__hal__conf_8h_a4b1a233981ef5d96551ea1f08d1a7ea8}{USE\+\_\+\+HAL\+\_\+\+CEC\+\_\+\+REGISTER\+\_\+\+CALLBACKS}}~0U /\texorpdfstring{$\ast$}{*} CEC register callback disabled       \texorpdfstring{$\ast$}{*}/
\item 
\#define \mbox{\hyperlink{stm32f4xx__hal__conf_8h_aab15bfcb9198618bda3d7e914193b466}{USE\+\_\+\+HAL\+\_\+\+CRYP\+\_\+\+REGISTER\+\_\+\+CALLBACKS}}~0U /\texorpdfstring{$\ast$}{*} CRYP register callback disabled      \texorpdfstring{$\ast$}{*}/
\item 
\#define \mbox{\hyperlink{stm32f4xx__hal__conf_8h_af9580ae862dcc02cee7822030c48d6b8}{USE\+\_\+\+HAL\+\_\+\+DAC\+\_\+\+REGISTER\+\_\+\+CALLBACKS}}~0U /\texorpdfstring{$\ast$}{*} DAC register callback disabled       \texorpdfstring{$\ast$}{*}/
\item 
\#define \mbox{\hyperlink{stm32f4xx__hal__conf_8h_a64a4d06cebee4009f08652637fbf161d}{USE\+\_\+\+HAL\+\_\+\+DCMI\+\_\+\+REGISTER\+\_\+\+CALLBACKS}}~0U /\texorpdfstring{$\ast$}{*} DCMI register callback disabled      \texorpdfstring{$\ast$}{*}/
\item 
\#define \mbox{\hyperlink{stm32f4xx__hal__conf_8h_a86882c5f53554e458434c836812093db}{USE\+\_\+\+HAL\+\_\+\+DFSDM\+\_\+\+REGISTER\+\_\+\+CALLBACKS}}~0U /\texorpdfstring{$\ast$}{*} DFSDM register callback disabled     \texorpdfstring{$\ast$}{*}/
\item 
\#define \mbox{\hyperlink{stm32f4xx__hal__conf_8h_ad3fd64734f71ef9c872f38dd0d0b8cb0}{USE\+\_\+\+HAL\+\_\+\+DMA2\+D\+\_\+\+REGISTER\+\_\+\+CALLBACKS}}~0U /\texorpdfstring{$\ast$}{*} DMA2D register callback disabled     \texorpdfstring{$\ast$}{*}/
\item 
\#define \mbox{\hyperlink{stm32f4xx__hal__conf_8h_a6c2182c3202253ba1a70c7d25122013c}{USE\+\_\+\+HAL\+\_\+\+DSI\+\_\+\+REGISTER\+\_\+\+CALLBACKS}}~0U /\texorpdfstring{$\ast$}{*} DSI register callback disabled       \texorpdfstring{$\ast$}{*}/
\item 
\#define \mbox{\hyperlink{stm32f4xx__hal__conf_8h_aa24a8d7886d3a497a868d5bf2417bfdf}{USE\+\_\+\+HAL\+\_\+\+ETH\+\_\+\+REGISTER\+\_\+\+CALLBACKS}}~0U /\texorpdfstring{$\ast$}{*} ETH register callback disabled       \texorpdfstring{$\ast$}{*}/
\item 
\#define \mbox{\hyperlink{stm32f4xx__hal__conf_8h_a0390418ff6315463b6ef161c63a69d43}{USE\+\_\+\+HAL\+\_\+\+HASH\+\_\+\+REGISTER\+\_\+\+CALLBACKS}}~0U /\texorpdfstring{$\ast$}{*} HASH register callback disabled      \texorpdfstring{$\ast$}{*}/
\item 
\#define \mbox{\hyperlink{stm32f4xx__hal__conf_8h_a560b53001fb58138f7da15dbda8f58a6}{USE\+\_\+\+HAL\+\_\+\+HCD\+\_\+\+REGISTER\+\_\+\+CALLBACKS}}~0U /\texorpdfstring{$\ast$}{*} HCD register callback disabled       \texorpdfstring{$\ast$}{*}/
\item 
\#define \mbox{\hyperlink{stm32f4xx__hal__conf_8h_a99be773f7f62b6277d1c87658e085725}{USE\+\_\+\+HAL\+\_\+\+I2\+C\+\_\+\+REGISTER\+\_\+\+CALLBACKS}}~0U /\texorpdfstring{$\ast$}{*} I2C register callback disabled       \texorpdfstring{$\ast$}{*}/
\item 
\#define \mbox{\hyperlink{stm32f4xx__hal__conf_8h_a940b1da88a7c3b2be040ff8bd05d2e7c}{USE\+\_\+\+HAL\+\_\+\+FMPI2\+C\+\_\+\+REGISTER\+\_\+\+CALLBACKS}}~0U /\texorpdfstring{$\ast$}{*} FMPI2C register callback disabled    \texorpdfstring{$\ast$}{*}/
\item 
\#define \mbox{\hyperlink{stm32f4xx__hal__conf_8h_a46f8aba8b355db501b426e3a82620e47}{USE\+\_\+\+HAL\+\_\+\+FMPSMBUS\+\_\+\+REGISTER\+\_\+\+CALLBACKS}}~0U /\texorpdfstring{$\ast$}{*} FMPSMBUS register callback disabled  \texorpdfstring{$\ast$}{*}/
\item 
\#define \mbox{\hyperlink{stm32f4xx__hal__conf_8h_a1bdc791c35b20c7188b3d74fd6c30ebf}{USE\+\_\+\+HAL\+\_\+\+I2\+S\+\_\+\+REGISTER\+\_\+\+CALLBACKS}}~0U /\texorpdfstring{$\ast$}{*} I2S register callback disabled       \texorpdfstring{$\ast$}{*}/
\item 
\#define \mbox{\hyperlink{stm32f4xx__hal__conf_8h_a4a459bcaa046998e6939fc66b0831e96}{USE\+\_\+\+HAL\+\_\+\+IRDA\+\_\+\+REGISTER\+\_\+\+CALLBACKS}}~0U /\texorpdfstring{$\ast$}{*} IRDA register callback disabled      \texorpdfstring{$\ast$}{*}/
\item 
\#define \mbox{\hyperlink{stm32f4xx__hal__conf_8h_a5b148dcae2bf8f576fc69a349794df4c}{USE\+\_\+\+HAL\+\_\+\+LPTIM\+\_\+\+REGISTER\+\_\+\+CALLBACKS}}~0U /\texorpdfstring{$\ast$}{*} LPTIM register callback disabled     \texorpdfstring{$\ast$}{*}/
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

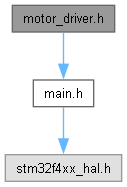
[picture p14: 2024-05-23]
docs/motor__driver_8h__incl.png

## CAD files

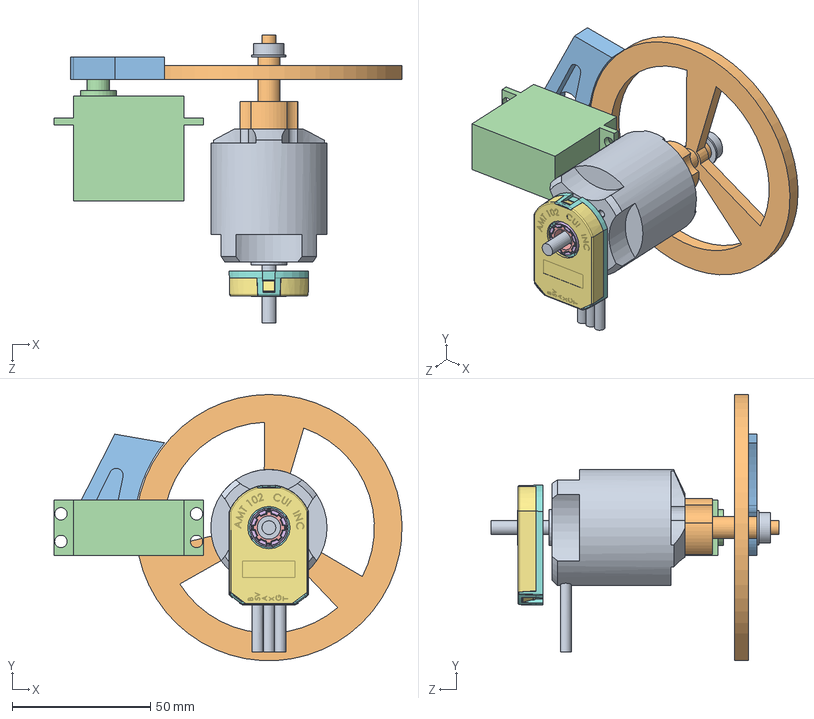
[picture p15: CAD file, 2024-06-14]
CAD/main.SLDASM
125.7 x 96.1 x 104.0 mm
wheel
motor
amt102-v_01
amt102-v_02
amt102-v_04
amt102-v_06
servo
servo_arm
motor_shaft
5x11x5mm_bearing

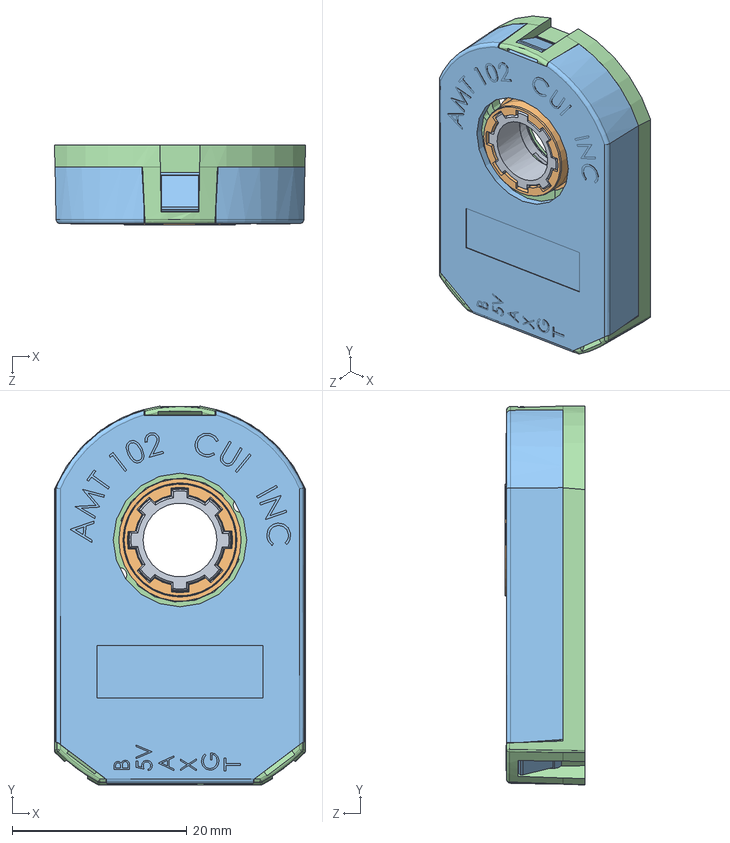
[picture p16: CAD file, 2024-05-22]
CAD/AMT102-V/amt102-v.SLDASM
28.8 x 43.4 x 9.15 mm
amt102-v_01
amt102-v_02
amt102-v_04
amt102-v_06

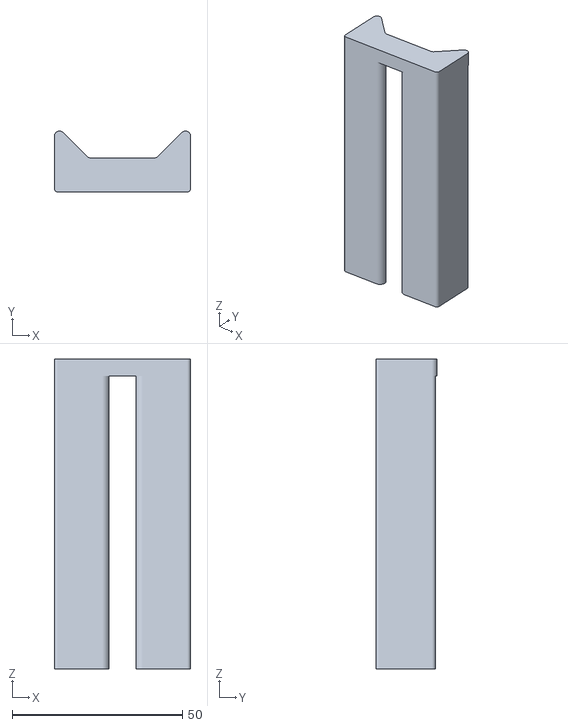
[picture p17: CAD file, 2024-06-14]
CAD/support_bracket.STL
40.0 x 17.9 x 91.0

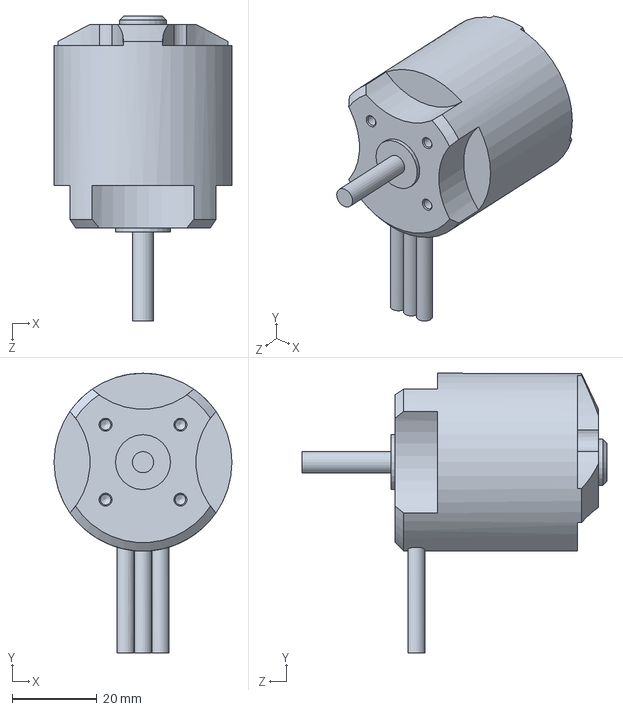
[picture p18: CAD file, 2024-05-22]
CAD/motor.SLDPRT
42.0 x 66.0 x 72.0 mm

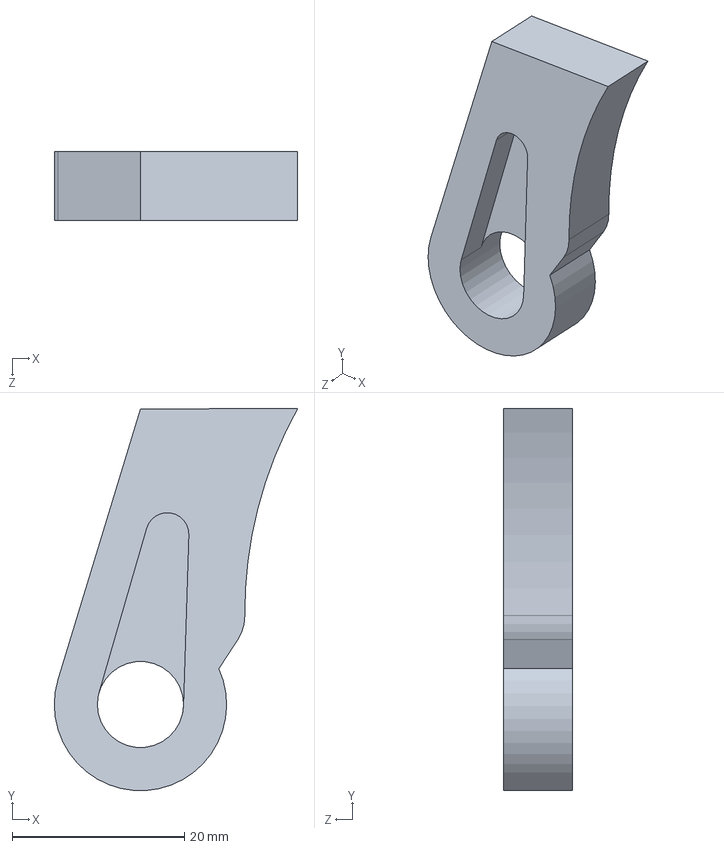
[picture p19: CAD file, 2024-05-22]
CAD/servo_arm.SLDPRT
28.2 x 44.3 x 8.00 mm

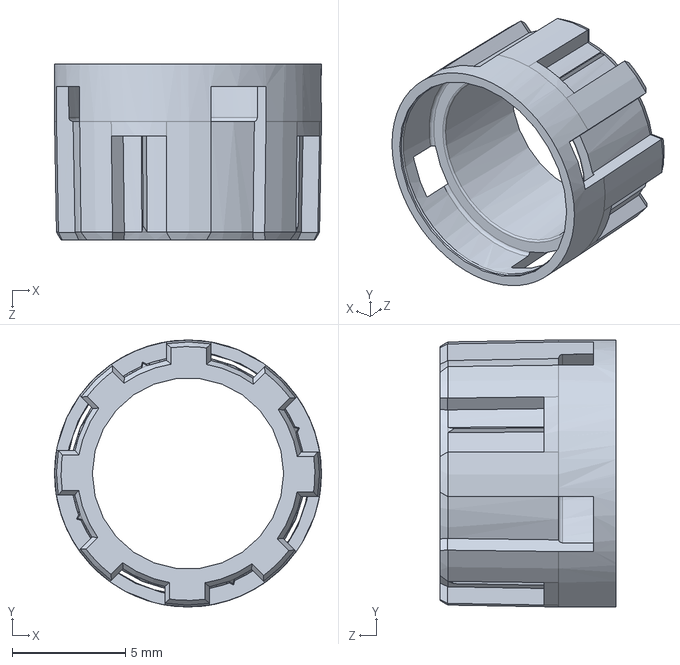
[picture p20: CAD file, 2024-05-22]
CAD/AMT102-V/amt102-v_06.SLDPRT
11.8 x 11.8 x 7.80 mm

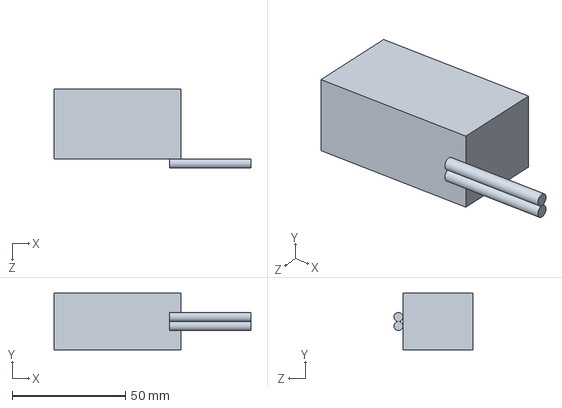
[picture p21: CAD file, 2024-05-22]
CAD/battery.SLDPRT
87.0 x 25.0 x 35.0 mm

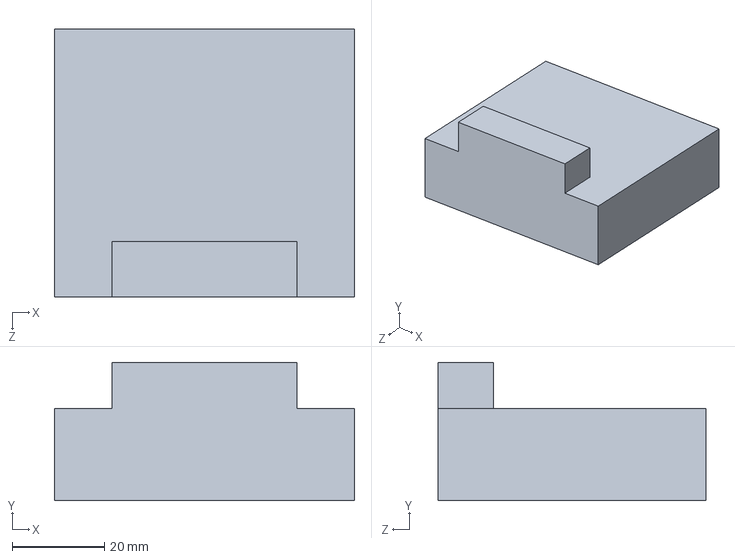
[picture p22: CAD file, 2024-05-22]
CAD/odrive.SLDPRT
65.0 x 30.0 x 58.0 mm

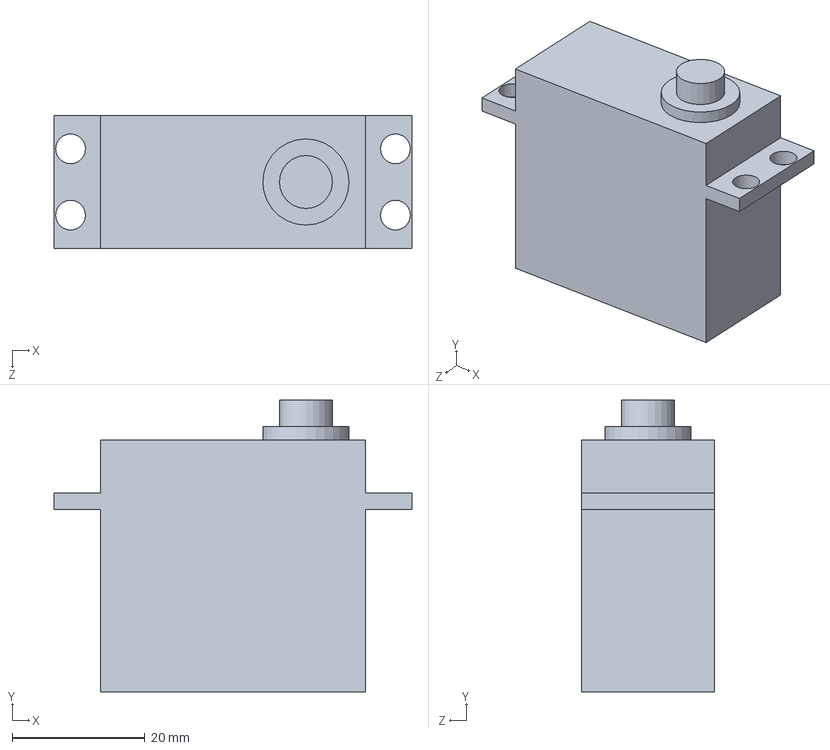
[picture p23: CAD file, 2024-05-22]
CAD/servo.SLDPRT
54.0 x 44.0 x 20.0 mm

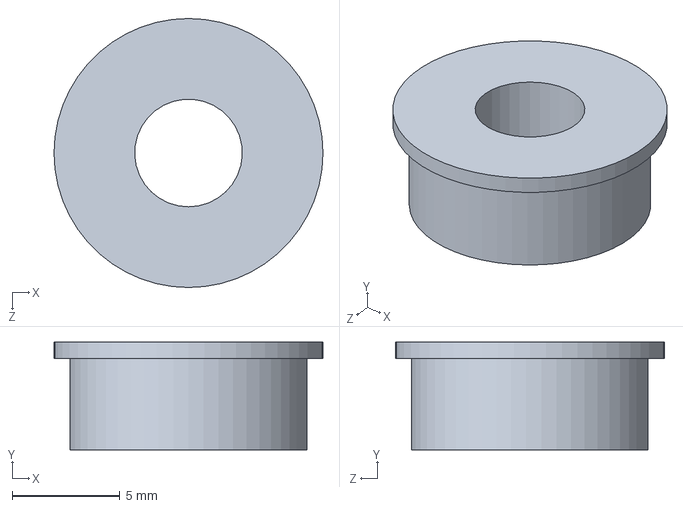
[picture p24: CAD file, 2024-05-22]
CAD/5x11x5mm_bearing.SLDPRT
12.5 x 5.00 x 12.5 mm

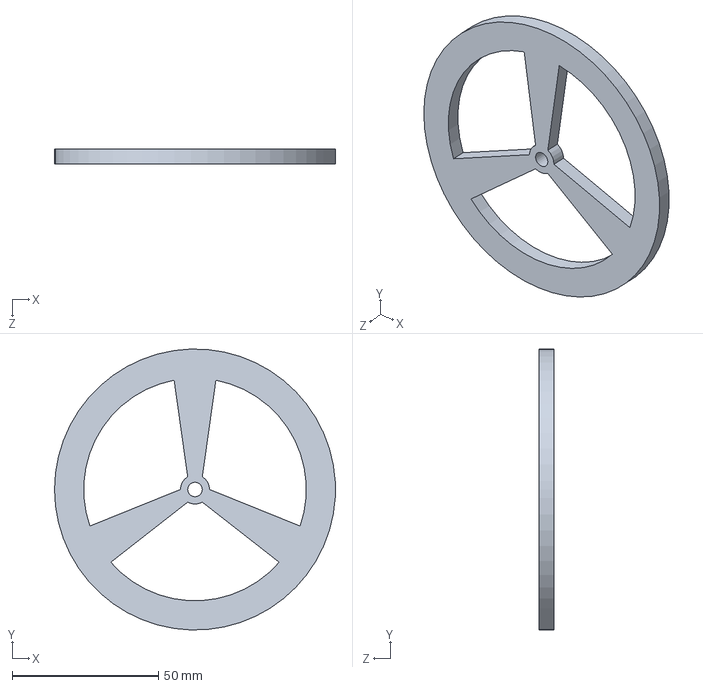
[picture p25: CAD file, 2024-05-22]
CAD/wheel.SLDPRT
96.2 x 96.2 x 5.00 mm

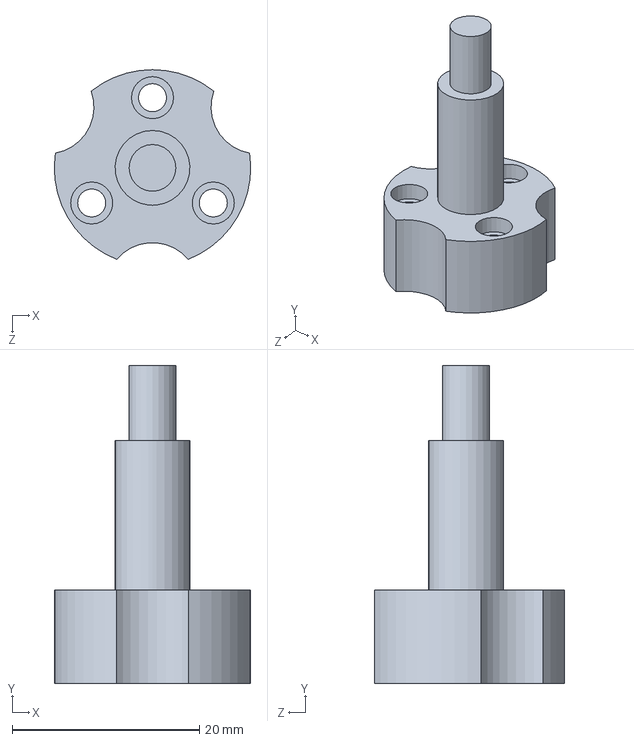
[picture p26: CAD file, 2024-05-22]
CAD/motor_shaft.SLDPRT
21.0 x 34.0 x 20.3 mm

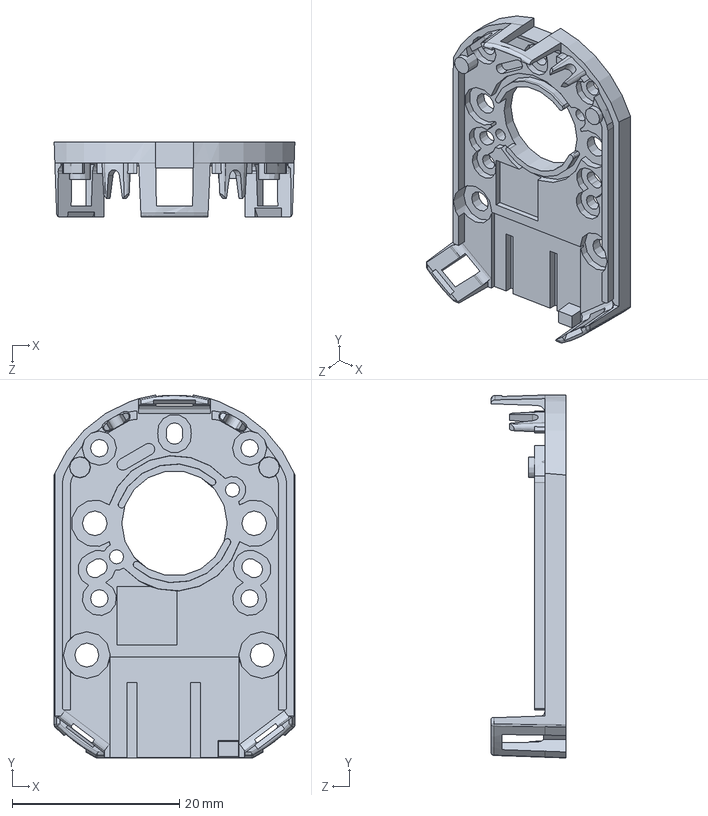
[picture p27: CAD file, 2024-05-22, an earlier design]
CAD/AMT102-V/amt102-v_01.SLDPRT
28.8 x 43.4 x 9.00 mm

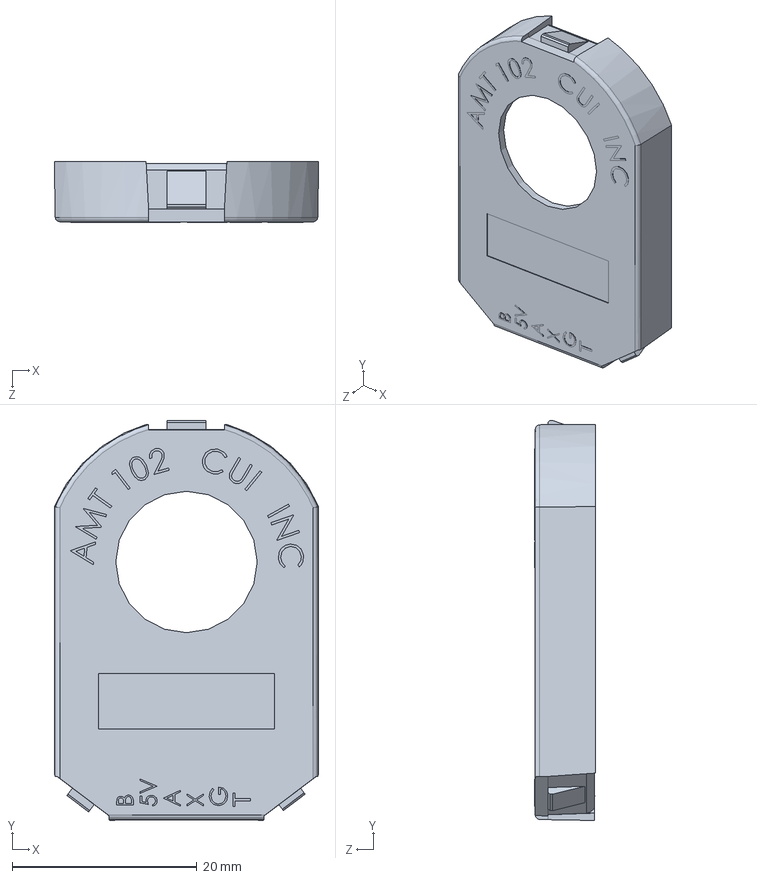
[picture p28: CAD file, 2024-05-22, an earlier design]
CAD/AMT102-V/amt102-v_02.SLDPRT
28.6 x 43.3 x 6.55 mm

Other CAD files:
CAD/AMT102-V/amt102-v_04.SLDPRT

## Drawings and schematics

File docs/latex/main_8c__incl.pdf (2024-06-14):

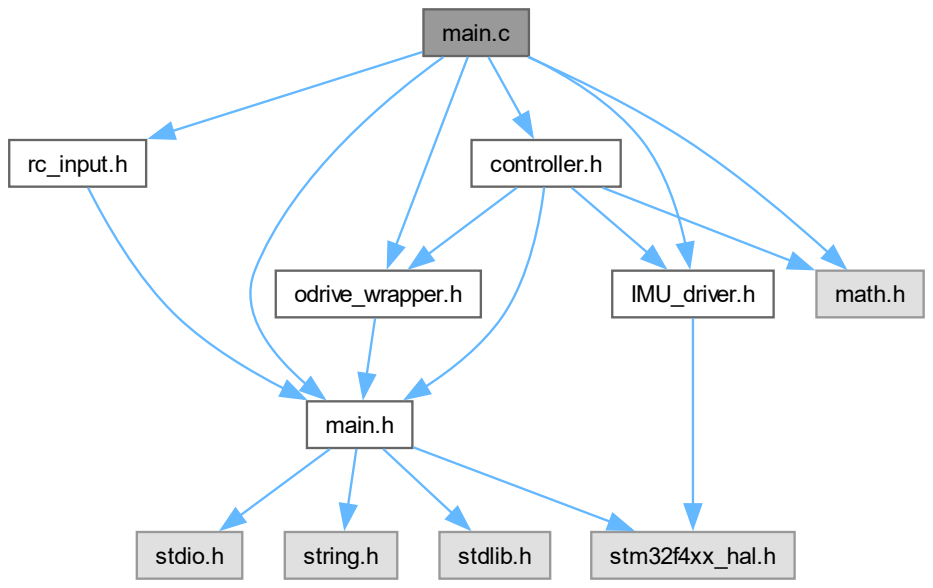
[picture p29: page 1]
main.c; main.h; odrive_wrapper.h; IMU_driver.h; controller.h; math.h; rc_input.h; stdio.h; string.h; stdlib.h; stm32f4xx_hal.h

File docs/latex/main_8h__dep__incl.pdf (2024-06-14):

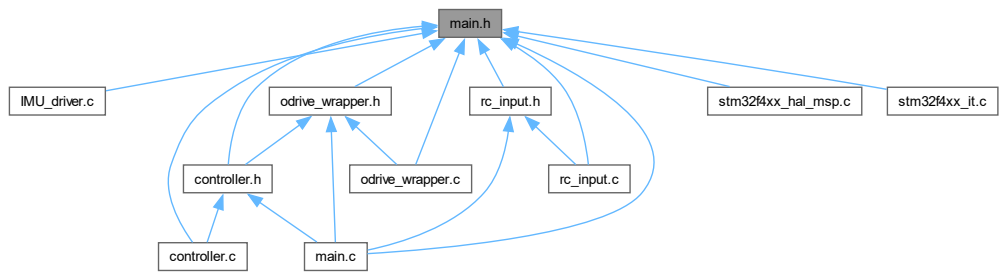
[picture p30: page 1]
main.h; IMU_driver.c; controller.c; controller.h; main.c; odrive_wrapper.c; odrive_wrapper.h; rc_input.c; rc_input.h; stm32f4xx_hal_msp.c; stm32f4xx_it.c

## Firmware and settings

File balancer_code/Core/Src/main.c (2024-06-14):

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
/* Includes ------------------------------------------------------------------*/
#include "main.h"

/* USER CODE BEGIN Includes */
#include "odrive_wrapper.h"
#include "IMU_driver.h"
#include "controller.h"
#include "rc_input.h"
#include <math.h>
/* USER CODE END Includes */

I2C_HandleTypeDef hi2c1;

TIM_HandleTypeDef htim1;
TIM_HandleTypeDef htim3;
TIM_HandleTypeDef htim4;
TIM_HandleTypeDef htim5;
TIM_HandleTypeDef htim11;

UART_HandleTypeDef huart2;
UART_HandleTypeDef huart6;

/* USER CODE BEGIN PV */

// comms test
/*
#define BUFFER_SIZE 5
uint8_t rxBuffer[BUFFER_SIZE];
uint8_t rxIndex = 0;
uint8_t char_in;
*/

// UART2 is laptop
// UART6 is odrive

// odrive obj
odrive_t odrive = {
		  .huart = &huart6
};

odrive_t laptop = {
		  .huart = &huart2
};

//creating IMU object
ICM_20948 IMU ={
		.hi2c = &hi2c1,
		.huart = &huart2 // uart to print data
};

extern uint8_t rxBuffer; // Receive buffer. max length of expected returned values.
extern uint8_t rxIndex; // init index at zero.
extern uint8_t responseFinishedFlag;
extern uint8_t receivedData;
extern char transmitBuffer;

volatile uint8_t IMU_rdy_flag = 0;
volatile uint8_t LED_rdy_flag = 0;
volatile uint8_t CTRL_rdy_flag = 0;

volatile float real_pos = 0;
volatile float sys_vel = 0;

/* USER CODE END PV */

void SystemClock_Config(void);
static void MX_GPIO_Init(void);
static void MX_I2C1_Init(void);
static void MX_USART2_UART_Init(void);
static void MX_TIM3_Init(void);
static void MX_USART6_UART_Init(void);
static void MX_TIM11_Init(void);
static void MX_TIM1_Init(void);
static void MX_TIM5_Init(void);
static void MX_TIM4_Init(void);
/**
  * @brief  The application entry point.
  * @retval int
  */
int main(void)
{

  /* MCU Configuration--------------------------------------------------------*/

  /* Reset of all peripherals, Initializes the Flash interface and the Systick. */
  HAL_Init();

  /* Configure the system clock */
  SystemClock_Config();

  /* Initialize all configured peripherals */
  MX_GPIO_Init();
  MX_I2C1_Init();
  MX_USART2_UART_Init();
  MX_TIM3_Init();
  MX_USART6_UART_Init();
  MX_TIM11_Init();
  MX_TIM1_Init();
  MX_TIM5_Init();
  MX_TIM4_Init();
  /* USER CODE BEGIN 2 */

  // start interrupts for timing tasks
  HAL_TIM_Base_Start_IT(&htim1);
  HAL_TIM_Base_Start_IT(&htim4);
  HAL_TIM_Base_Start_IT(&htim5);

  // start receiving
  start_receive_string(&odrive);

  HAL_UART_Transmit(&huart2, (uint8_t*)"\033c", strlen("\033c"), HAL_MAX_DELAY);

  ODRIVE_Reboot(&odrive);
  HAL_Delay(10000);

  ODRIVE_ClearErrors(&odrive);

  IMU_init(&IMU);


  // battery voltage readout
  //uint8_t* voltage = ODRIVE_GetVBus(&odrive);
  //char new_mess[50];
  //int mess_len = sprintf(new_mess, "Received VBus: %s\r\n", voltage);
  //HAL_UART_Transmit(laptop.huart, (uint8_t*)new_mess, mess_len, HAL_MAX_DELAY);


  /* USER CODE END 2 */

  /* Infinite loop */
  /* USER CODE BEGIN WHILE */
  while (1)
  {
    /* USER CODE END WHILE */

    /* USER CODE BEGIN 3 */

    /*
	// speed requests
	ODRIVE_SetVelocity(&odrive, 0, 2);
	ODRIVE_SetVelocity(&laptop, 0, 2);
	HAL_Delay(2000);
	ODRIVE_SetVelocity(&odrive, 0, 0.5);
	ODRIVE_SetVelocity(&laptop, 0, 0.5);
	HAL_Delay(2000);
	*/

	//IMU_read_accel(&IMU);
	//IMU_read_gyro(&IMU);

	// LED task
	if (LED_rdy_flag == 1) {
		LED_rdy_flag = 0;

		HAL_GPIO_TogglePin(GPIOB, GPIO_PIN_15);

	}


	// IMU read task
    if (IMU_rdy_flag ==  1) {
        IMU_rdy_flag = 0;

    	pos_spd new_IMU_out = calculate_IMU_Angle(&IMU);

    	real_pos = new_IMU_out.position - 90;
    	sys_vel = new_IMU_out.speed;

    	char ctrl_msg[50];
        sprintf(ctrl_msg, "SYS ANGLE: %.4f     ", real_pos);
        HAL_UART_Transmit(laptop.huart, (uint8_t*)ctrl_msg, strlen(ctrl_msg), HAL_MAX_DELAY);

        sprintf(ctrl_msg, "ANG_VEL: %.4f     \r\n", new_IMU_out.speed);
        HAL_UART_Transmit(laptop.huart, (uint8_t*)ctrl_msg, strlen(ctrl_msg), HAL_MAX_DELAY);

    }

    // Controller task
    if (CTRL_rdy_flag == 1) {
    	CTRL_rdy_flag = 0;

    	uint8_t* feedback = ODRIVE_GetFeedback(&odrive, 0);

    	float motor_pos, motor_vel;
    	extractFloats(feedback, &motor_pos, &motor_vel);

    	update_control(&odrive, real_pos, sys_vel, motor_vel);
    	//char feedback_mess[50];
        //int feedback_mess_len = sprintf(feedback_mess, "MOTOR_FEEDBACK: %s\r\n", feedback);
        //HAL_UART_Transmit(laptop.huart, (uint8_t*)feedback_mess, feedback_mess_len, HAL_MAX_DELAY);

    }



  }
  /* USER CODE END 3 */
}

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
/* USER CODE BEGIN 4 */

void HAL_UART_RxCpltCallback(UART_HandleTypeDef *huart)
{
	ODRIVE_Receive_Callback(huart, &odrive);
}

void HAL_TIM_PeriodElapsedCallback(TIM_HandleTypeDef*htim){
	if (htim == &htim1){ // check the timer value
		IMU_rdy_flag = 1;
	}
	else if (htim == &htim4){
		CTRL_rdy_flag = 1;
	}
	else if (htim == &htim5){
		LED_rdy_flag = 1;
	}
}


/* USER CODE END 4 */
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


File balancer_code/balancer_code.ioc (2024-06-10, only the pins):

Mcu.UserName=STM32F411RETx
PA13.Signal=SYS_JTMS-SWDIO
PA14.Signal=SYS_JTCK-SWCLK
PA2.Signal=USART2_TX
PA3.Signal=USART2_RX
PA7.Signal=S_TIM3_CH2
PB15.Signal=GPIO_Output
PB3.Signal=SYS_JTDO-SWO
PB5.Signal=GPXTI5
PB6.Signal=I2C1_SCL
PB7.Signal=I2C1_SDA
PB9.Signal=S_TIM11_CH1
PC6.Signal=USART6_TX
PC7.Signal=USART6_RX

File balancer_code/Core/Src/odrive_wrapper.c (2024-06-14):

/*
 * odrive_wrapper.c
 *
 *  Created on: May 20, 2024
 *      Author: Aidan
 */
/// @file odrive_wrapper.c
/// @brief Provides functions for interfacing with an external ODrive controller.
///< Implements the ASCII protocol as defined by ODrive: https://docs.odriverobotics.com/v/latest/manual/ascii-protocol.html
#include "main.h"
#include "odrive_wrapper.h"

uint8_t rxBuffer[BUFFER_SIZE]; 		// Receive buffer. max length of expected returned values.
uint8_t rxIndex = 0; 				// init index at zero.
uint8_t responseFinishedFlag = 0;
uint8_t receivedData[BUFFER_SIZE];

/**
 * Sends ASCII command to reboot ODrive.
 * @param p Pointer to an ODrive object.
 */
void ODRIVE_Reboot(odrive_t *p)
{
	char message[50];
    int len = sprintf(message, "sr\r\n");
    HAL_UART_Transmit(p->huart, (uint8_t*)message, len, HAL_MAX_DELAY);
}

/**
 * Sends ASCII command to clear errors on ODrive.
 * @param p Pointer to an ODrive object.
 */
void ODRIVE_ClearErrors(odrive_t *p)
{
	char message[50];
    int len = sprintf(message, "sc\r\n");
    HAL_UART_Transmit(p->huart, (uint8_t*)message, len, HAL_MAX_DELAY);
}

/**
 * Sends ASCII command to send position setpoint to ODrive.
 * @param p Pointer to an ODrive object.
 * @param motor_number Motor number on ODrive. Typically 0.
 * @param position Position setpoint
 * @param velocity_lim Velocity limit
 * @param torque_lim Torque limit
 */
void ODRIVE_SetPosition(odrive_t *p, int motor_number, float position, float velocity_lim, float torque_lim)
{
	char message[50];
    int len = sprintf(message, "q %d %.3f %.3f %.3f\r\n", motor_number, position, velocity_lim, torque_lim);
    HAL_UART_Transmit(p->huart, (uint8_t*)message, len, HAL_MAX_DELAY);
}

/**
 * Sends ASCII command to send position setpoint with feedforward ODrive.
 * @param p Pointer to an ODrive object.
 * @param motor_number Motor number on ODrive. Typically 0.
 * @param position Position setpoint
 * @param velocity_feedforward Velocity feedforward value.
 * @param current_feedforward Current feedforward value.
 */
void ODRIVE_SetPositionFF(odrive_t *p, int motor_number, float position, float velocity_feedforward, float current_feedforward)
{
	char message[50];
    int len = sprintf(message, "p %d %.3f %.3f %.3f\r\n", motor_number, position, velocity_feedforward, current_feedforward);
    HAL_UART_Transmit(p->huart, (uint8_t*)message, len, HAL_MAX_DELAY);
}

/**
 * Sends ASCII command to send velocity setpoint to ODrive.
 * @param p Pointer to an ODrive object.
 * @param motor_number Motor number on ODrive. Typically 0.
 * @param velocity Velocity setpoint.
 */
void ODRIVE_SetVelocity(odrive_t *p, int motor_number, float velocity)
{
	char message[50];
    int len = sprintf(message, "v %d %.3f\r\n", motor_number, velocity);
    HAL_UART_Transmit(p->huart, (uint8_t*)message, len, HAL_MAX_DELAY);
}

/**
 * Sends ASCII command to send torque setpoint to ODrive.
 * @param p Pointer to an ODrive object.
 * @param motor_number Motor number on ODrive. Typically 0.
 * @param torque Torque setpoint.
 */
void ODRIVE_SetTorque(odrive_t *p, int motor_number, float torque)
{
	char message[50];
    int len = sprintf(message, "c %d %.3f\r\n", motor_number, torque);
    HAL_UART_Transmit(p->huart, (uint8_t*)message, len, HAL_MAX_DELAY);
}

/**
 * Sends ASCII command to get current position and velocity from ODrive.
 * @param p Pointer to an ODrive object.
 * @param motor_number Motor number on ODrive. Typically 0.
 */
uint8_t* ODRIVE_GetFeedback(odrive_t *p, int motor_number)
{
	char message[50];
	int len = sprintf(message, "f %d \r\n", motor_number);
	HAL_UART_Transmit(p->huart, (uint8_t*)message, len, HAL_MAX_DELAY);

	uint8_t* response = 0;
	while((response = getReceivedString(p)) == NULL)
	{
	  // wait for a response to be completed
	  HAL_Delay(1);
	}
	//HAL_UART_Transmit(p->huart, (uint8_t*)response, strlen(response), HAL_MAX_DELAY);
	return response;
}

/**
 * Sends ASCII command to get VBUS voltage from ODrive.
 * Used mainly as a test to see if we can send and receive UART commands.
 * @param p Pointer to an ODrive object.
 */
uint8_t* ODRIVE_GetVBus(odrive_t *p)
{
	char message[50];
	int len = sprintf(message, "r vbus_voltage \r\n");
	HAL_UART_Transmit(p->huart, (uint8_t*)message, len, HAL_MAX_DELAY);

	uint8_t* response = 0;
	while((response = getReceivedString(p)) == NULL)
	{
	  // wait for a response to be completed
	  HAL_Delay(1);
	}
	return response;
}

/**
 * Sends ASCII command to check calibrated status ODrive.
 * I think this one is broken.
 * @param p Pointer to an ODrive object.
 */
uint8_t* ODRIVE_IsCalibrated(odrive_t *p)
{
	char message[50];
	int len = sprintf(message, "r axis0.motor.is_calibrated \r\n");
	HAL_UART_Transmit(p->huart, (uint8_t*)message, len, HAL_MAX_DELAY);

	uint8_t* response = 0;
	while((response = getReceivedString(p)) == NULL)
	{
	  // wait for a response to be completed
	  HAL_Delay(1);
	}
	return response;
}

/**
 * Sends ASCII command to ODrive.
 * @param p Pointer to an ODrive object.
 * @param param[] Parameter to write to, in string format.
 */
void ODRIVE_WriteParam(odrive_t *p, char param[])
{
	char message[50];
    int len = sprintf(message, "w %s \r\n", param);
    HAL_UART_Transmit(p->huart, (uint8_t*)message, len, HAL_MAX_DELAY);
}

/**
 * Receives ASCII command from ODrive.
 * @param p Pointer to an ODrive object.
 * @param param[] Parameter to read from, in string format.
 */
uint8_t* ODRIVE_ReadParam(odrive_t *p, char param[])
{
	char message[50];
	int len = sprintf(message, "r %s \r\n", param);
	HAL_UART_Transmit(p->huart, (uint8_t*)message, len, HAL_MAX_DELAY);

	uint8_t* response = 0;
	while((response = getReceivedString(p)) == NULL)
	{
	  // wait for a response to be completed
	  HAL_Delay(1);
	}
	return response;
}

/**
 * Sends ASCII command to reboot ODrive.
 * @param p Pointer to an ODrive object.
 */
uint8_t* getReceivedString(odrive_t *p)
{
	static uint8_t receivedDataCopy[BUFFER_SIZE]; // create a copied variable that is returned

	if (responseFinishedFlag)
	{
		responseFinishedFlag = 0;
		memcpy(receivedDataCopy, receivedData, strlen((char*)receivedData));
		return receivedDataCopy; // return the copied variable
	}
	else
	{
		return NULL;
	}
}

/**
 * Starts receiving a new string via UART.
 * Sets the buffer index to zero and sets up HAL_UART_Receive correctly for the ODrive object.
 * @param p Pointer to an ODrive object.
 */
void start_receive_string(odrive_t *p)
{
	rxIndex = 0; // reset the buffer index
    memset(rxBuffer, 0, sizeof(rxBuffer)); // Clear the received string buffer
    HAL_UART_Receive_IT(p->huart, &rxBuffer[rxIndex], 1); // Start receiving data
}
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

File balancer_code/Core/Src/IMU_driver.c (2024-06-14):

/*
 * IMU_driver.c
 *
 *  Created on: Jun 2, 2024
 *      Author: Sydney
 */
/// @file IMU_driver.c
/// @brief Implements a few features of the ICM20948 via I2C.
#include "main.h"
#include "IMU_driver.h"
#include "stm32f4xx_hal.h"
#include <string.h>

// buffer for uart communication
char msg[50];

int16_t accel_x_raw, accel_y_raw, accel_z_raw; // raw accelerometer data
float accel_x, accel_y, accel_z;
int16_t gyro_x_raw, gyro_y_raw, gyro_z_raw; // raw gyro data
float gyro_x, gyro_y, gyro_z;

uint8_t raw_data[6]; //for use with the above


//function definitions for the IMU

/**
 * Initializes the ICM20948 IMU.
 * Checks I2C connection, reads the WHO_AM_I register, and scans device address for verification purposes. Prints debugging messages through uart.
 * @param ICM_20948 Pointer to an IMU object
 */
void IMU_init(ICM_20948*p_IMU){

	HAL_StatusTypeDef ret = HAL_I2C_IsDeviceReady(p_IMU->hi2c, ICM20948_I2C_ADDR, 1, 100); // i2c pointer & because we want the address
    	  	  	  	  	  	  	  	  	  	  	  	  	  	  	  	  	 // addrr is 11001, added 0 for the function to read
    	  	  	  	  	  	  	  	  	  	  	  	  	  	  	  	  	 // trials: number of times to try the connection
    	  	  	  	  	  	  	  	  	  	  	  	  	  	  	  	  	 // timout in ms
    if (ret == HAL_OK)
      {
    	  HAL_UART_Transmit(p_IMU->huart, (uint8_t*)"\r\n imu: connected ", 19, HAL_MAX_DELAY); // ensure string length is correct
      }
      else
      {
    	  HAL_UART_Transmit(p_IMU->huart, (uint8_t*)"\r\n imu: no connection", 21, HAL_MAX_DELAY);
      }


    // checking the WHO_AM_I register
    uint8_t check;
    uint8_t data;

    // Check WHO_AM_I register
    HAL_I2C_Mem_Read(p_IMU->hi2c, ICM20948_I2C_ADDR, WHO_AM_I_REG, I2C_MEMADD_SIZE_8BIT, &check, 1, HAL_MAX_DELAY);
    if (check == 0xEA) // WHO_AM_I should return 0xEA for ICM-20948
    {
    	HAL_UART_Transmit(p_IMU->huart, (uint8_t*)"\r\n ICM-20948 found\r\n", 20, HAL_MAX_DELAY);
         sprintf(msg, "WHO_AM_I reads 0x%02X\r\n", check);
         HAL_UART_Transmit(p_IMU->huart, (uint8_t*)msg, strlen(msg), HAL_MAX_DELAY);
         // Wake up the sensor (clear sleep mode bit)
         data = 0x01;
         HAL_I2C_Mem_Write(p_IMU->hi2c, ICM20948_I2C_ADDR, PWR_MGMT_1_REG, I2C_MEMADD_SIZE_8BIT, &data, 1, HAL_MAX_DELAY);
     }
     else
     {
    	 HAL_UART_Transmit(p_IMU->huart, (uint8_t*)"ICM-20948 not found\r\n", 21, HAL_MAX_DELAY);
      }


     //I2C scanner
     char info[] = "Scanning I2C bus...\r\n";
     HAL_UART_Transmit(p_IMU->huart, (uint8_t*)info, strlen(info), HAL_MAX_DELAY);

     for (uint8_t addr = 1; addr < 128; addr++)
     {
    	 if (HAL_I2C_IsDeviceReady(p_IMU->hi2c, addr << 1, 1, 10) == HAL_OK)
         {
    		 char msg[32];
    		 sprintf(msg, "Found device at 0x%02X\r\n", addr);
    		 HAL_UART_Transmit(p_IMU->huart, (uint8_t*)msg, strlen(msg), HAL_MAX_DELAY);
         } else {
    		 char msg[50];
    		 sprintf(msg, "No device found\r\n");
    		 //HAL_UART_Transmit(p_IMU->huart, (uint8_t*)msg, strlen(msg), HAL_MAX_DELAY);
         }
     }
}

/**
 * Reads IMU acceleration data.
 * Accesses the relevant registers via I2C and returns a triplet of float data scaled appropriately.
 * @param ICM_20948 Pointer to an IMU object
 */
AccelData IMU_read_accel(ICM_20948*p_IMU){
	AccelData accel_data = {0};

	if (HAL_I2C_Mem_Read(p_IMU->hi2c, ICM20948_I2C_ADDR, ACCEL_XOUT_H, I2C_MEMADD_SIZE_8BIT, raw_data, 6, HAL_MAX_DELAY) == HAL_OK)
	{
		accel_x_raw = (int16_t)(raw_data[0] << 8 | raw_data[1]);
	    accel_y_raw = (int16_t)(raw_data[2] << 8 | raw_data[3]);
	    accel_z_raw = (int16_t)(raw_data[4] << 8 | raw_data[5]);

	    // take the raw readings, divide by sensitivity, multiply by 9.81 to get reading m/s^2 reading
	    accel_x = (float)accel_x_raw * GRAV / ACCEL_FS;
	    accel_y = (float)accel_y_raw * GRAV / ACCEL_FS;
	    accel_z = (float)accel_z_raw * GRAV / ACCEL_FS;

	    accel_data.accel_x = accel_x_raw * GRAV / ACCEL_FS;
	    accel_data.accel_y = accel_y_raw * GRAV / ACCEL_FS;
	    accel_data.accel_z = accel_z_raw * GRAV / ACCEL_FS;

	    // output the data in m/s^2
	    // took out the \r\n for testing
	    //sprintf(msg, "Accel X: %.4f, Y: %.4f, Z: %.4f     ", accel_data.accel_x, accel_data.accel_y, accel_data.accel_z);
	    //HAL_UART_Transmit(p_IMU->huart, (uint8_t*)msg, strlen(msg), HAL_MAX_DELAY);

	}
	else
	{
		HAL_UART_Transmit(p_IMU->huart, (uint8_t*)"Error reading accel data\r\n", 26, HAL_MAX_DELAY);
	    accel_data.accel_x = 0;
	    accel_data.accel_y = 0;
	    accel_data.accel_z = 0;
	}

	return accel_data;
}

/**
 * Reads IMU gyro data.
 * Accesses the relevant registers via I2C and returns a triplet of float data scaled appropriately.
 * @param ICM_20948 Pointer to an IMU object
 */
GyroData IMU_read_gyro(ICM_20948*p_IMU){
	GyroData gyro_data = {0};

	if (HAL_I2C_Mem_Read(p_IMU->hi2c, ICM20948_I2C_ADDR, GYRO_XOUT_H, I2C_MEMADD_SIZE_8BIT, raw_data, 6, HAL_MAX_DELAY) == HAL_OK)
	{

		gyro_x_raw = (int16_t)(raw_data[0] << 8 | raw_data[1]);
	    gyro_y_raw = (int16_t)(raw_data[2] << 8 | raw_data[3]);
	    gyro_z_raw = (int16_t)(raw_data[4] << 8 | raw_data[5]);

	    // take the raw readings, divide by sensitivity. data in deg/s
	    gyro_x = (float)gyro_x_raw / GYRO_FS_SEL;
	    gyro_y = (float)gyro_y_raw / GYRO_FS_SEL;
	    gyro_z = (float)gyro_z_raw / GYRO_FS_SEL;

	    gyro_data.gyro_x = gyro_x_raw / GYRO_FS_SEL;
	    gyro_data.gyro_y = gyro_y_raw / GYRO_FS_SEL;
	    gyro_data.gyro_z = gyro_z_raw / GYRO_FS_SEL;

	    // output the data in deg/s
	    //sprintf(msg, "Gyro X: %.4f, Y: %.4f, Z: %.4f      ", gyro_data.gyro_x, gyro_data.gyro_y, gyro_data.gyro_z);
	    //HAL_UART_Transmit(p_IMU->huart, (uint8_t*)msg, strlen(msg), HAL_MAX_DELAY);

	}
	else
	{
		HAL_UART_Transmit(p_IMU->huart, (uint8_t*)"Error reading gyro data\r\n", 25, HAL_MAX_DELAY);
	    gyro_data.gyro_x = 0;
	    gyro_data.gyro_y = 0;
	    gyro_data.gyro_z = 0;
	}

	return gyro_data;
}

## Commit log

2024-05-09 first push with H7 MCU
    [12402012E212A.PcbLib, 12402012E212A.SchLib, 507_Part_Footprints.PcbLib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]
2024-05-22 lots of changes, mainly adding doxygen
    [507_Part_Footprints.PcbLib, 507_Parts.SchLib, 5x11x5mm_bearing.SLDPRT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]
2024-06-09 working uart and MCU on PCB but no i2c yet.
    [MCU_Extras.SchDoc]
2024-06-10 imu kinda working now
2024-06-14 Updating documentation and mainpage.
    [main.SLDASM, support_bracket.STL]
